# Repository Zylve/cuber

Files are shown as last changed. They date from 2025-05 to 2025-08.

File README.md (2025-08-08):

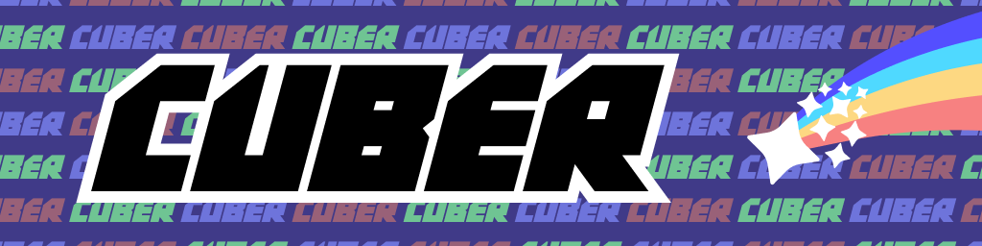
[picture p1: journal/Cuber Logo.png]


# Cuber
Cuber is an automatic rubiks cube robot that can read the state of a 3x3 cube and solve it using servo motors.

Cuber was funded by and built for Hack Club's [Highway](https://highway.hackclub.com) program. You can read my journal [here](./JOURNAL.md). 

Want to make your own? Find documentation on how to build it [here](./docs/README.md).

I've spent over 120 hours designing and building Cuber. Read my thoughts [here](./REFLECTION.md). (TBA)

## 3D Model
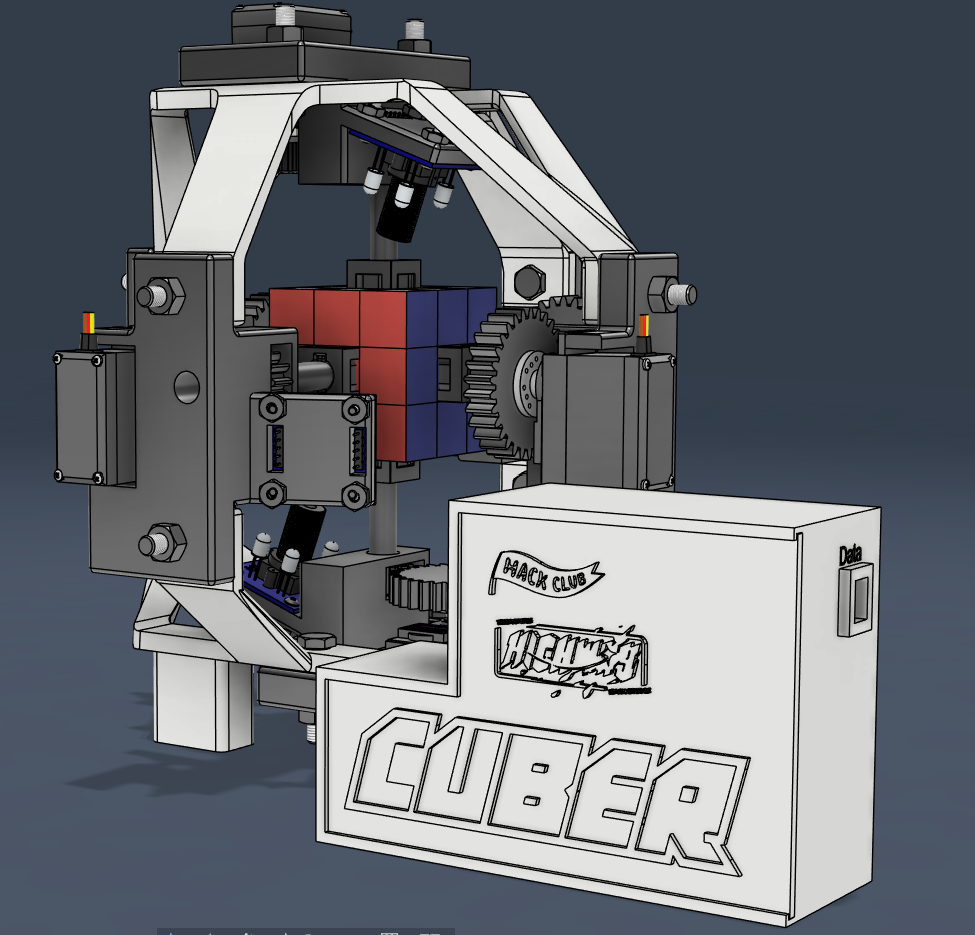
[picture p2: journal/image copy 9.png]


## Wiring Schematic
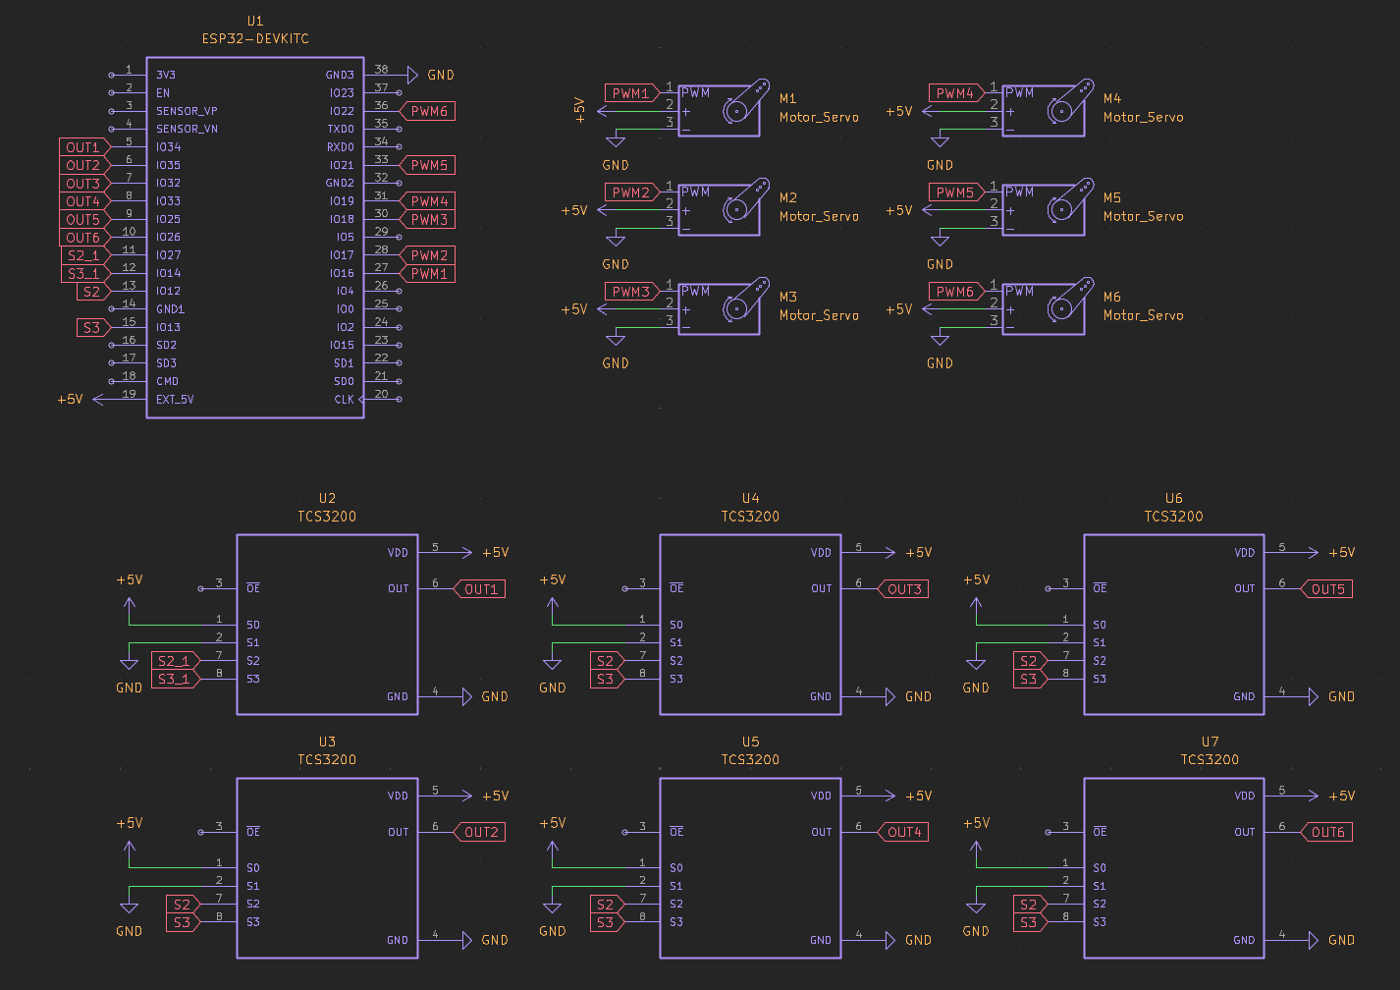
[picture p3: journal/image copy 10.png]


## Physical Project
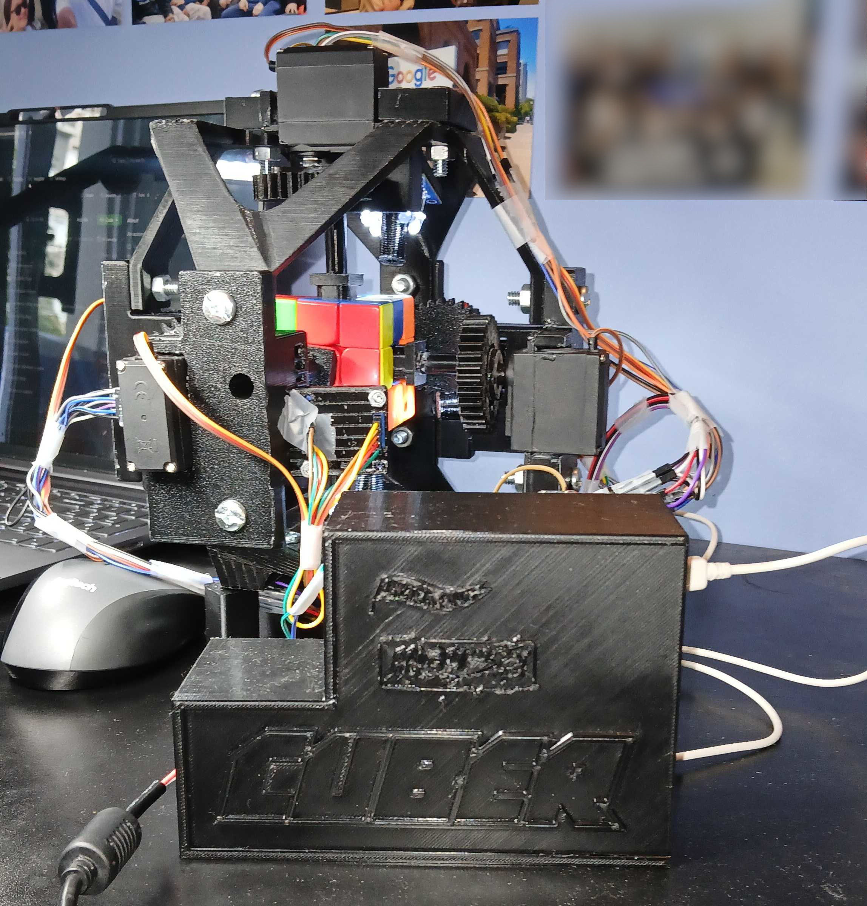
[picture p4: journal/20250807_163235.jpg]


## Bill of Materials
| Item | Amount | Cost (CAD) |
|---|---|---|
| [Esp32 Dev-Board](https://www.aliexpress.com/item/1005006651936701.html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) | 1 | $6.24 |
| [MG996R 180° Stepper Motor](https://www.aliexpress.com/item/1005007032811340.html) | 6 | $32.67 |
| [TCS3200 Colour Sensor](https://www.aliexpress.com/item/1005001625710961.html) | 6 | $24.00 |
| [Assorted Dupont Wires](https://www.aliexpress.com/item/1005004647016228.html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) | 50 | $7.22 |
| [Splice Terminals](https://www.aliexpress.com/item/1005008417745708.html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) | 10 | $8.67 |
| [5V 10A Power Supply](https://www.aliexpress.com/item/4000229912671.html) | 1 | $15.48 |
| [Super Glue](https://www.aliexpress.com/item/1005008238433750.html) | 15g | $24.21
| 1/4-20 & 4-40 Bolts and Nuts | 12 each | $5.00
| PLA Filament | 250g | $6.50 |
| | | |
| **Total** | | **$129.99**|
| **Total USD** | | **$94.56** |

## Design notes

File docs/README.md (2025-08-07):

# Documentation

## Notes
All colours in this project have an ID associated with it. Here are the mappings:
| Colour | ID (0-index) | ID (1-index) | Face |
|:---:|:---:|:---:|:----:|
| White  | 0 | 1 | U |
| Red | 1 | 2 | R |
| Green  | 2 | 3 | F |
| Yellow | 3 | 4 | D |
| Orange | 4 | 5 | L |
| Blue | 5 | 6 | B |

## Hardware
All parts of Cuber were printed in PLA with standard Cura and supports enabled.

The pinion that grabs the cube and the gear were attached to the shaft via press-fit and super glue. The gear attached directly to the servo was aligned using physical guides in the print and super glued.

The colour sensors are attached to the gearbox via 4-40 bolts hardware. This can be done via super glue as well.

The gearboxes are attached to the main nets via 1/4-20 hardware.

## Electronics


Cuber was wired using the following schematic. To prevent larges amounts of current going through the ESP32, you must distribute power directly from the wall. I used wagos to do this, but you can choose a different method. You can view my distribution [here](./WIRING.md).

The S0 & S1 pins on the colour sensors are wired to their secondary set of VCC and GND pins. The S2 & S3 connections are distributed from a single ESP32 pin. All other signal wires are point-to-point to the ESP32.

Note that there exists a separate point-to-point connection for the colour sensor on the up face (S2_1, S3_1). This is because I ran out of wagos.

## Software
### Building & Uploading
Clone the repository.
```bash
git clone https://github.com/Zylve/cuber.git
cd cuber
```

Prepare the platformio project
```bash
pio run
```

To upload the code to the ESP32, connect via USB
```bash
pio run -t upload
```

Setup the python environment
```bash
cd ko
python -m venv .
./bin/pip install pyserial # linux/mac
./Scripts/pip install pyserial # windows
```

### Setting up the code.
Set the correct pins in `include/pins.h`.

#### Servo Calibration
Disable the C_MAIN flag, enable the C_SERVO_INPUT flag and set the servo ID in `include/config.h`. Connect via serial monitor and you will be able to prompt the servo to turn between 0 and 180 degrees. In `src/servos.cpp` you will have to set the correct angles.

```cpp
// Servo 1
ServoConfig servo_config_1 = {
    .axis_positions = {
        {2, 42, 78, 117},
        {2, 38, 78, 117},
        {2, 38, 78, 117},
        {2, 38, 72, 117}
    },
    .square_positions = {20, 35, 56, 71, 93, 109, 132, 149},
    .square_ids = {2, 3, 6, 9, 8, 7, 4, 1} // Different because of the net in the algorithm :/
};
```

The `.axis_positions` is the angle each servo needs to drive to to reach a certain position. The array is in the format of `[from][to]`. Setting the values properly will allow for faster turns as the servo will not undershoot due to friction.

The `.square_positions` is the angle each servo needs to drive to for the colour sensor to point towards each square on the cube. To calibrate, test each angle in order from `.axis_positions[0][0]`, and find the angle that causes the servo to stop such that the dark point of the colour sensor tube is in the middle of the square.

`.square_ids` is the ID of the square mapped to the `.square_positions` array. Note that this is different for the first servo because of how the kociemba library takes input.

#### Colour Sensor Calibration
Set the appropriate values in `src/colours.cpp` for each sensor.

```cpp
ColourConfig config_1 = { // White face sensor
    .white = { // White colour
        .red = {0.30, 0.37},
        .green = {0.30, 0.37},
        .blue = {0.30, 0.37}
    },
    .red = { // Red colour
        .red = {0.48, 1.00},
        .green = {0.00, 0.25},
        .blue = {0.00, 0.20}
    },
    // ...

    .colour_map = {
        .red = {2500, 38000},
        .green = {3600, 24000},
        .blue = {3400, 18000}
    }
};
```

You will have to take the raw readings from the sensors via `sensors[i]->get_colour_raw()`. Rotate each colour on the cube through the sensor and mark down the minimum and maximum values for each colour channel. Set these values as your `.colour_map`.

With the `.colour_map` set, take the normalized readings via `sensors[i]->get_colour_normalized()`. Rotate each colour through various positions and set the proper bands for each channel in each colour.

Note that this will take a lot of trial and error. It took me over 20 hours to get it right. It is still not perfect but I am honestly tired of calibrating the sensors.

Reset the flags in `include/config.h` to enable the main program again.

#### Python Solver
Set the correct serial port in `ko/main.py`
```python
esp32 = serial.Serial(port="COM7", baudrate=9600, timeout=0.1)
```

### Usage

#### Solving
Connect Cuber to wall power and connect the ESP32 via USB to your computer. Upload the program with the main flag enabled.

On a system with port access, run the python script
```bash
./bin/python main.py # linux/mac
./Scripts/python main.py # windows
```
Once connected, Cuber will start reading the faces of the cube. Once it is finished, it will prompt you to enter the colours for any squares that it failed to read. It will display the location (U2, R5, etc) and prompt for the colour (U, R, F, D, L, B). Read through the [notes](#notes) and the [Colour Routine](./COLOURS.md) file for information on that.

After all the colours are entered, it will run the kociemba algorithm, will start running the solution while displaying the moves on the serial monitor.

#### Scrambling
Disconnect Cuber from wall power. Manually scramble the cube. Take note that once connected to power the servos will zero to their starting positions.

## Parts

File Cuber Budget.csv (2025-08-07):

Item | Amount | Cost (CAD)
Esp32 Dev-Board | 1 | $6.24
MG996R 180° Stepper Motor | 6 | $32.67
TCS3200 Colour Sensor | 6 | $24.00
Assorted Dupont Wires | 50 | $7.22
Splice Terminals | 10 | $8.67
Super Glue | 15g | $24.21
5V 10A Power Supply | 1 | $15.48
1/4-20 & 4-40 Bolts and Nuts | 12 each | $5.00
PLA Filament | 250g | $6.50
Total |  | $129.99
Total USD |  | $94.56

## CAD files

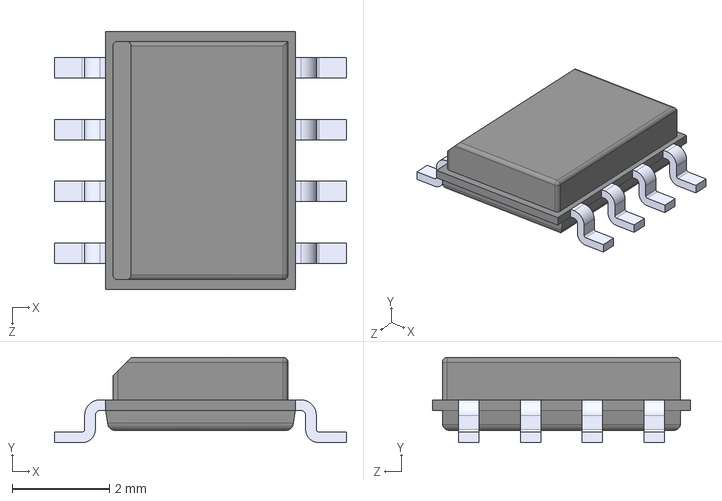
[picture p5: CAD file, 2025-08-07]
CAD/Wiring Diagram/TCS3200/TCS3200.step
6.00 x 1.75 x 5.30 mm

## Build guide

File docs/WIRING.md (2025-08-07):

# Wiring Guide
(This is currently just a reference for myself so if it doesn't make sense, that's okay.)

Colours:
- White: 0 (1)
- Red: 1 (2)
- Green: 2 (3)
- Yellow: 3 (4)
- Orange: 4 (5)
- Blue: 5 (6)

Other:
- 5V: V
- GND: G
- Servo: M
- Colour Sensor: C
- Signal: S# (S0, S1, ...)

5V:
- ESP32
- V0-0,2 (White & Green):
    - V0-0:
        - V0-0M
        - V0-0C
    - V0-2:
        - V0-2M
        - V0-2C
- V1-1,3 (Red & Blue):
    - V1-1:
        - V1-1M
        - V1-1C
    - V1-3:
        - V1-3M
        - V1-3C
- V2-4,5 (Orange & Yellow):
    - V2-4:
        - V2-4M
        - V2-4C
    - V2-5:
        - V2-5M
        - V2-5C

GND:
- ESP32
- G0-0,2 (White & Green):
    - G0-0:
        - G0-0M
        - G0-0C
    - G0-2:
        - G0-2M
        - G0-2C
- G1-1,3 (Red & Blue):
    - G1-1:
        - G1-1M
        - G1-1C
    - G1-3:
        - G1-3M
        - G1-3C
- G2-4,5 (Orange & Yellow):
    - G2-4:
        - G2-4M
        - G2-4C
    - G2-5:
        - G2-5M
        - G2-5C

Signal:
- Signal has no specific routings so we don't care about differentiating each wire.

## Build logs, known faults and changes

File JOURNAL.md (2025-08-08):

---
title: "Cuber"
author: "Vuk"
description: "An automatic Rubik's Cube solver"
created_at: "2024-05-17"
---

### Total Time: 116 hours
---

# May 15th: Started work!
Cooked up my idea and started researching the parts lying around in my kit and the school shop.

### Time today: 1 hour
### Time total: 1 hour

# May 17th:
Okay so basically I set up the platformio dev environment and got my esp32 driving an MG996R stepper motor.

https://github.com/user-attachments/assets/8cf88195-3297-4feb-9b49-cdf6550582a8

I've been wanting to create something like this for a while and I bought these components several months ago but never got around to seriously starting work on it. (And now it looks like Purdue beat me to it lol.)

Anyway I think the best way to properly begin this is to setup some goals for ***Cuber:***
- Create an automatic motorized Rubik's Cube solver.
- Have it automatically detect the initial state of the cube using colour sensors.
- Implement an algorithm like *Kociemba's* to solve the cube.
- Have an automatic scrambler to allow continuous action.
- 3D print a custom case to house components, that allows for easy access to the cube.

Wow that is a lot of goals haha.

To keep the kinematics of the cube simple, I will use a similar approach to the students at Purdue and MIT: 6 motors, one for each face of the  (no full cube rotations). To allow for access to the cube, I will allow the housing for each motor to swing out like a flower, letting me swap the cube in and out.

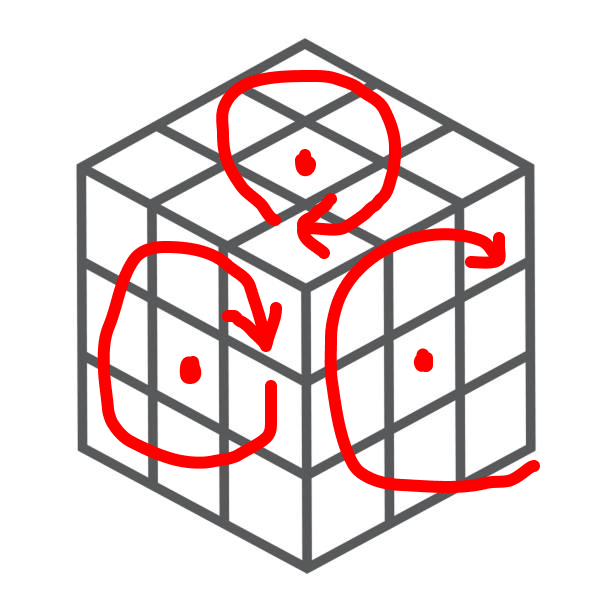
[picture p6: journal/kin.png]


I got 6 TCS3200 colour sensors from my school, and the idea is that one could cover each face of the cube on the corner, and rotate the face at 30° intervals to detect all 12 stickers.

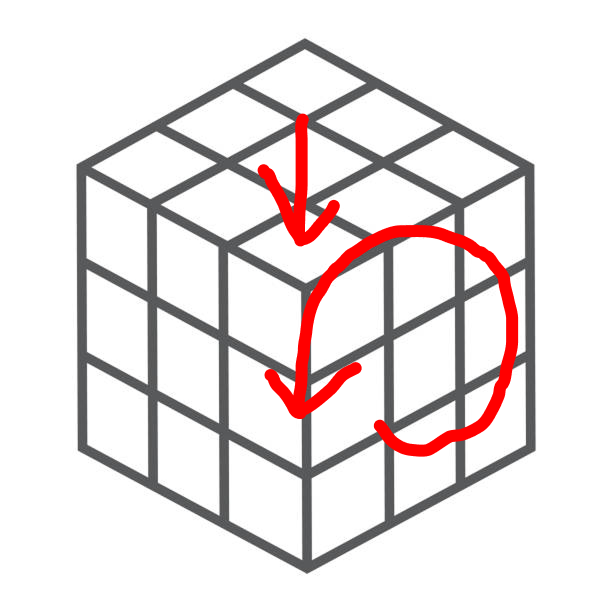
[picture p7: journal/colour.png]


I then imported the MG996R into Fusion 360 and designed a pinion for the Rubiks cube. It will drive the cube sides by slotting into the middle piece. This is when I realized that the motor spline is to small for my 3D printer to print. Instead, I will use the injection molded pinion that came with the motors, and probably superglue the pinion to it or smt idk.

<p float="left">
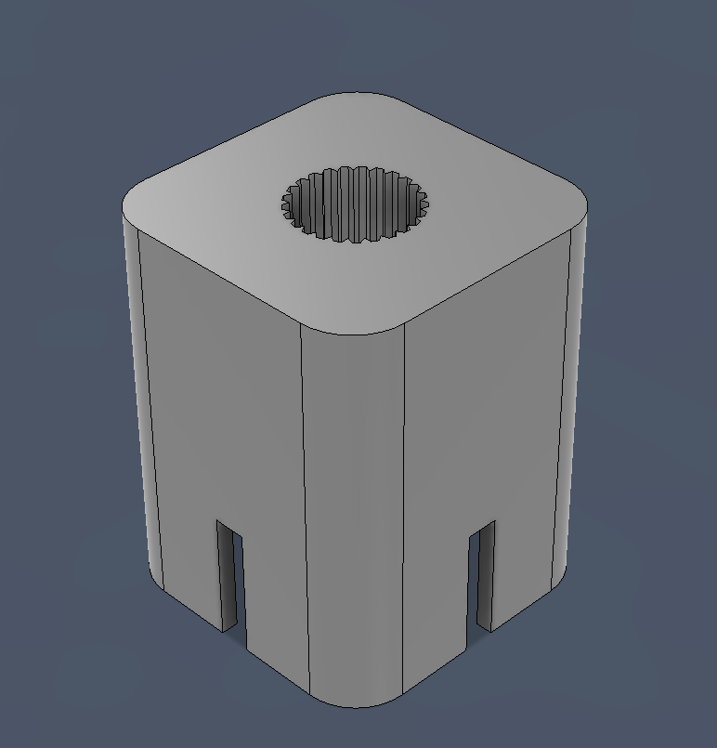
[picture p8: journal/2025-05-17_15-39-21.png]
    
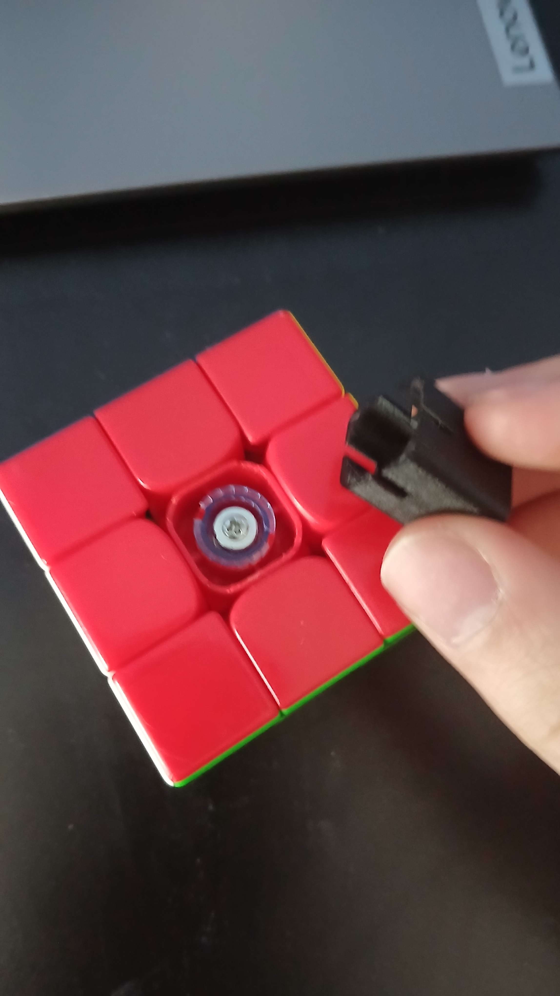
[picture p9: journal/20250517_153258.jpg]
    
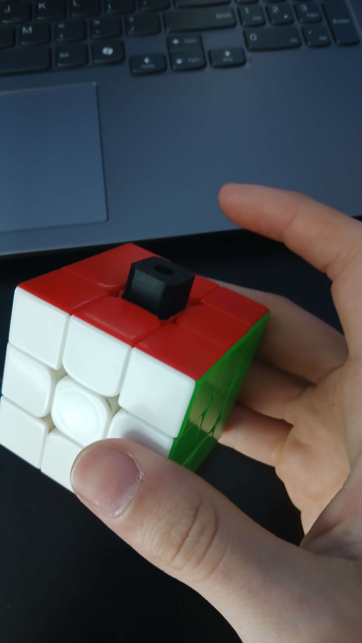
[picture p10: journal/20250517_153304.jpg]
    
</p>

### Time today: 4 hours
### Time total: 5 hours

# May 19th:
Spent like 30 minutes today trying to make PlatformIO actually useable.

I played with my prototype pinion a bit and learned that I need to apply a ton of normal force to allow the sides to rotate.

###### No force (top) vs. force (bottom)
https://github.com/user-attachments/assets/cadc4695-f0eb-4065-a3e3-c17ea3f0df7f

https://github.com/user-attachments/assets/0a5ce550-07eb-4adf-b740-79804e6239e9

I will need to loosen my cube a lot for this, but not so much that it explodes in your face. Lubricant is also needed, I don't know what type to use though. I can buy some specialized stuff from SpeedCubeShop or just douse the cube in some machine oil from my school's shop lol.

I haven't had a lot of time these past couple days but hopefully I will have some more soon!

### Time today: 1 hour
### Time total: 6 hours

# May 23rd:
Finally got some spare time! Jumped into Fusion today and designed a prototype gearbox for the motor & pinion.

Because the version of the MG996R I have has only 180° of rotation, I need to make a step up to allow for full range of motion. I went with a 1:2.5 gear ratio via a 30T pinion and a 12T gear. Not gonna lie the MG996R has a ton of torque—I did the math from the specsheet and I could go up to like 1:8 or something.

Anyway, the 1:2.5 ratio works as all of the angles I need are whole numbers.

<!-- Image.png -->
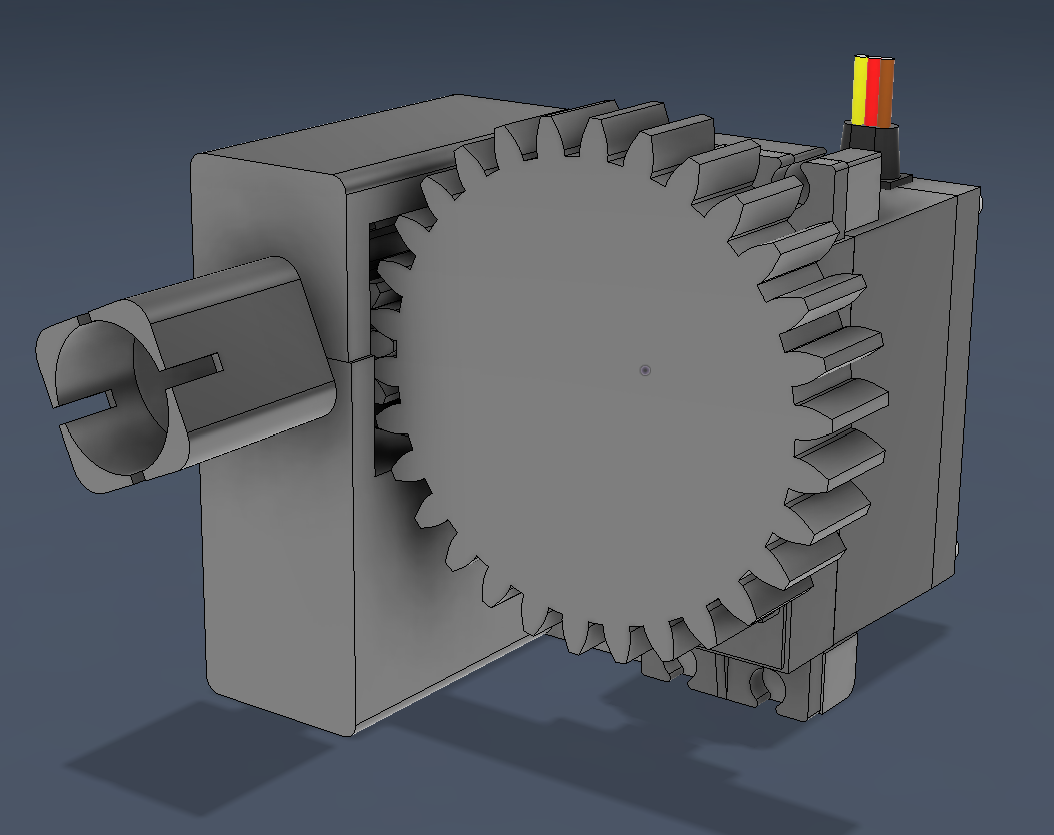
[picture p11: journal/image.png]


I'll be able to 3D print this over the weekend and test it out. If it works, I'll be able to attach 6 of these together to create a full robot. I'm still thinking about how to get the cube in and out though. The flower idea I mentioned early is probably too complex. I'll maybe make the top motor attached via a bolt that you can screw in and out. 

But now that we know we need a large normal force, we may have difficulty getting the cube in and out. When I have time I'll fiddle around with my pinion and see how much play there is and if it would be possible to twist the cube out. Otherwise we may need multiple motors to be unscrewable.

### Time today: 2 hours
### Time total: 8 hours

# May 24th & 25th:
Printed the gearbox. Turns out I suck at superglueing stuff together. Note to future self: sand the prints before gluing lmao.

Got it rotating and stuff. But I'm browning out the ESP32 on just a single stepper motor. Tomorrow I'll be able to take it to school and test it with an actual power supply.

https://github.com/user-attachments/assets/a11832de-1fdf-4844-b957-5d1f5c20488e

### Time this weekend: 4 hours
### Time total: 12 hours

# May 30th

So whats up. I tested the jig with a power supply and theres a couple things I learned:
- I need to make it stiffer so that the gears dont twist out.
- I suck at estimating tolerances.

For most of my testing time, the pieces of the cube were catching on each other, so I had to tighten the cube faces down. It was able to rotate the sides of the cube, but it was quite innacurate due to how much tolerance there was in the pinion and the gears.

I originally created a glue down cover for the pinion to rotate in, but my friend suggested that I make the shaft slide in and have the pinion be press fit.

### Time today: 1 hour
### Time total: 13 hours

# May 31st

Printed some tolerance tests.
- Print in place: 0.5mm
- Print out of place: 0.5mm
- Press fit: 0.3mm

Also designed a new pinion to better fit the cube. Reduced the tolerance between the pinion and the walls of the piece, and made it wrap around the corners. Not sure if the corner pieces actually do anything but maybe it increases the torque lever arm 🤷‍♂️.

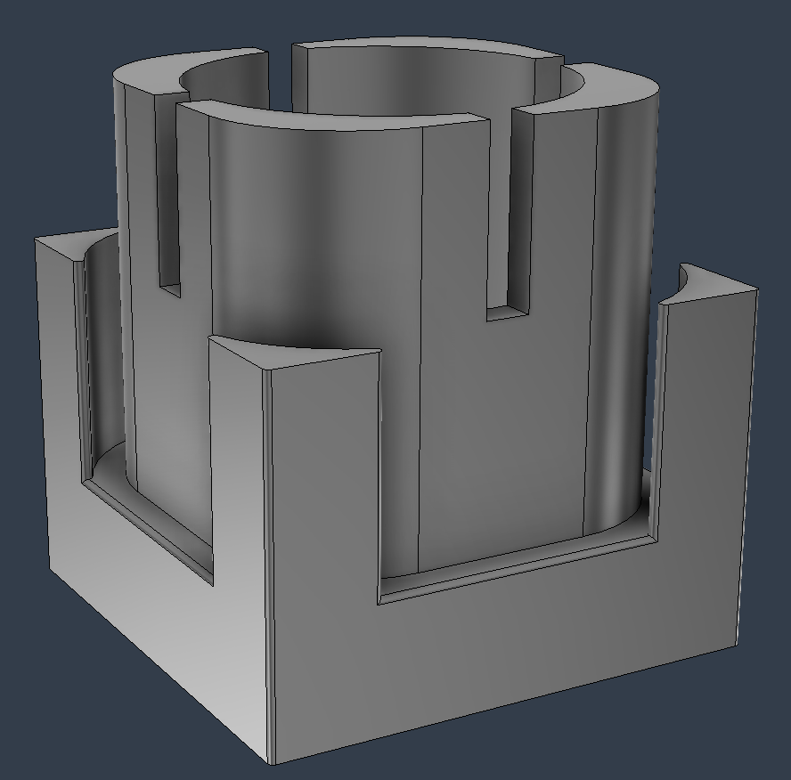
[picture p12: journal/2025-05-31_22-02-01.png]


### Time today: 3 hours
### Time total: 16 hours

# June 1st
Printed out the new gearbox and assembled it together. I need to update it a little as its too close to the face of the cube and the other sides of the cube can't actually rotate lol.

### Time today: 2 hours
### Time total: 18 hours

# June 2nd
Brought it to school and tested it out. Works much better with a lot more backlash. I can still reduce the last bit of it by adding a shaft to the pinion gear, keeping it from rocking side to side. Other than that, its pretty sweet. Something I've noticed is that for some reason the motor isn't linear. 0-90 is the same as 90-180, but 180-270 is much smaller. All stuff that can be changed in software.

https://github.com/user-attachments/assets/d39e9d64-2d36-401b-b0da-273edd4b6365

Hopefully v3 will be the final version of the gearbox. Once I confirm that works then I can start cadding the full assembly.

### Time today: 2 hours
### Time total: 20 hours

# June 6th
Spliced this power supply to power my esp32 and motors. It's 5V 10A, and each motor draws 2A maximum. Hooked it up and it works! I also looked into the specs of the jumper wires I was using and i could power up to 2 motors at a time. (22 AWG, 4A).



### Time today: 1 hour
### Time total: 21 hours

# June 7th
Started playing with the colour sensors. I tried using a library and wasted hours getting it to work. I instead settled to just doing all the fancy stuff manually. I got it able to differentiate between red, green, and blue, but I really need to calibrate the values and tune the thresholds it if I want accurate colours. I think I might need to do this for all 6 sensors.

Colour sensors pmo.

### Time today: 4 hours
### Time total: 25 hours

# June 8th
Dude the colour sensor works. IT WORKS.

I took min and max values for red, green, and blue, and then used this funky map function I found to map it to 0-255. I then used colour normalization to get the ratios of the colours (brightness independent). I then measured each side of the cube, getting the RGB ranges from right up against the cube to about 2 inches away. I could then just iterate over all my colours to find out which RGB band it falls into.

So excited to get this working. I will probably have to recalibrate it when I make the assembly, and also do it for 5 other sensors :(

However, now I know how to do it, so it should be faster next time!

From now I want to focus on integrating a sensor mount into the gearbox, and combining everything into a single 6 motor assembly. I will probably also have to make a wiring diagram. These colour sensors require a lot of pins, (5 exactly) but two of them (the ones that set the frequency) can be shared across all of them, saving 10 pins.

https://github.com/user-attachments/assets/c96f8a81-6cd7-4bb0-83de-4ab9377df998

### Time today: 2 hours
### Time total: 27 hours

# June 9th

Extended the drive shaft so that the cube wouldnt be blocked by the gearbox when turning. Added a mount for the colour sensor to the gearbox. I then also added some mounting holes and arranged the 6 gearboxes into an assembly.

It's really coming together!

I need to make the "net" that connects the 6 gearboxes together. The net will go on the inside of the gearboxes so that you can undo the bolts and just take them out without any maneuvering I also want to figure out how to make the wiring nice. It's gonna be so cooked because of how much there will be. I need 8 wires per gearbox (48 total) + more for splitting my power and ground. At the bottom of the assembly I can make a case for the ESP32. It might even be a good idea to make some buttons for control ("start", "stop"). But yeah. It's gonna be so good.

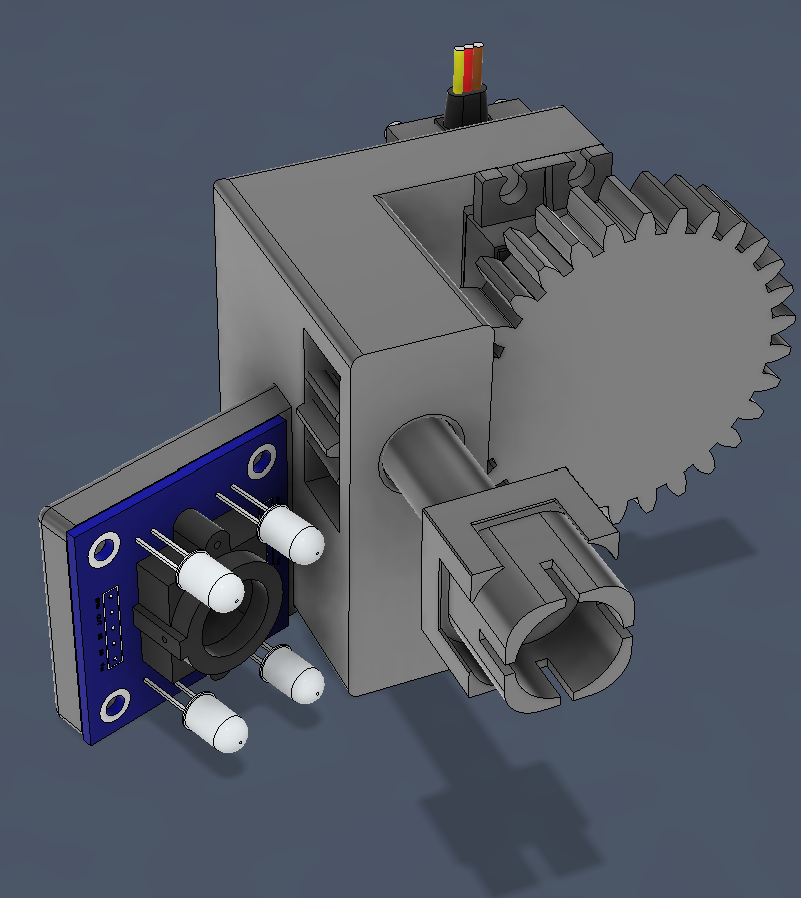
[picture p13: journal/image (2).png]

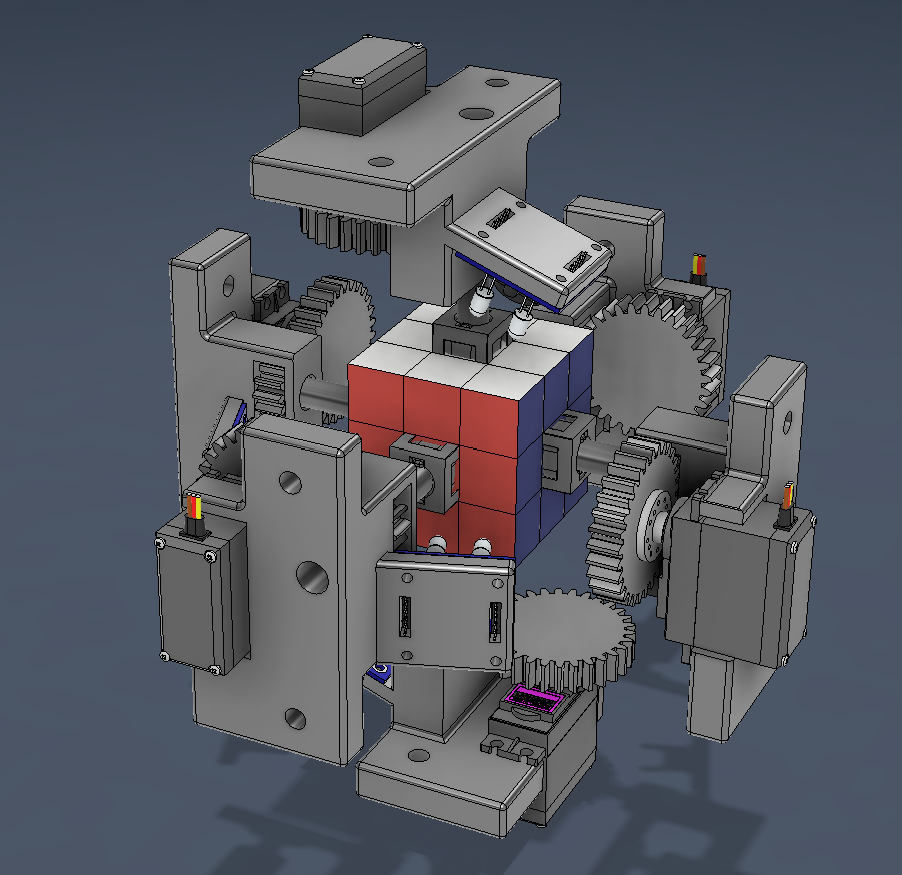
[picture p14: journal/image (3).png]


### Time today: 4 hours
### Time total: 31 hours

# June 10th
Holy lock in.

Made some "nets" that connects the gearboxes together, and a box to store all the electronics. The gearboxes mount to the net via 1/4-20 bolts, and when you unscrew them you can just take it right out with minimal fuss.

The CAD is mostly finished at this point. I had to make a few small modifications to get the colour sensor to fit.

I then made the wiring schematic in Fusion. It turned out a lot cleaner than I expected, but jesus it is a lot of wires. There will be lots of splicing and soldering to do for VBUS, GND, and sensor pins.

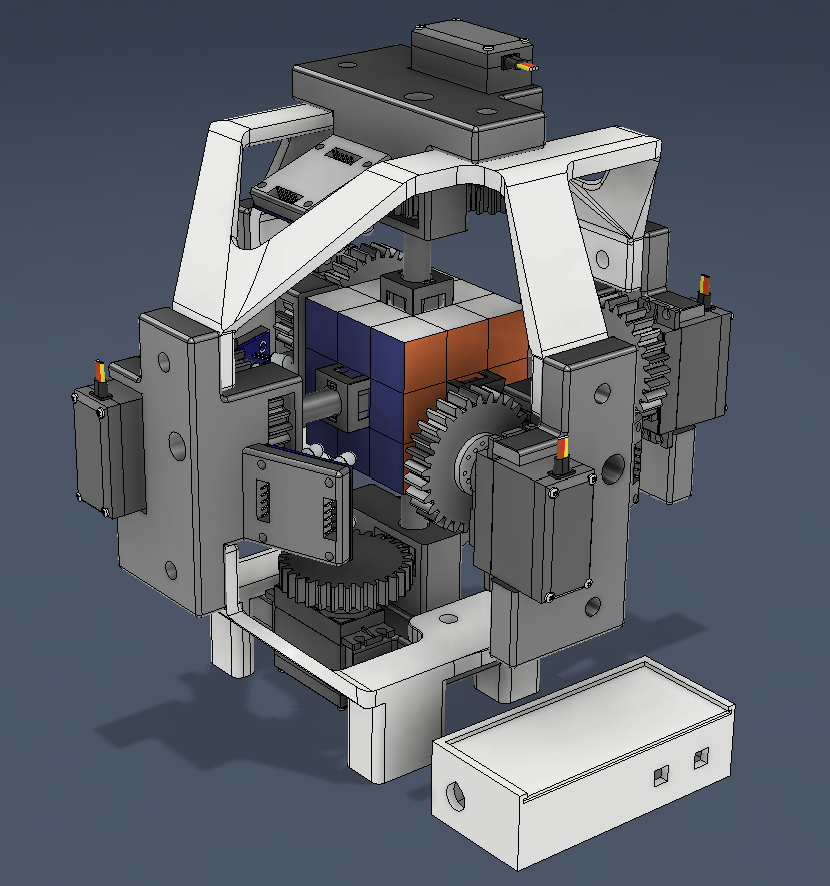
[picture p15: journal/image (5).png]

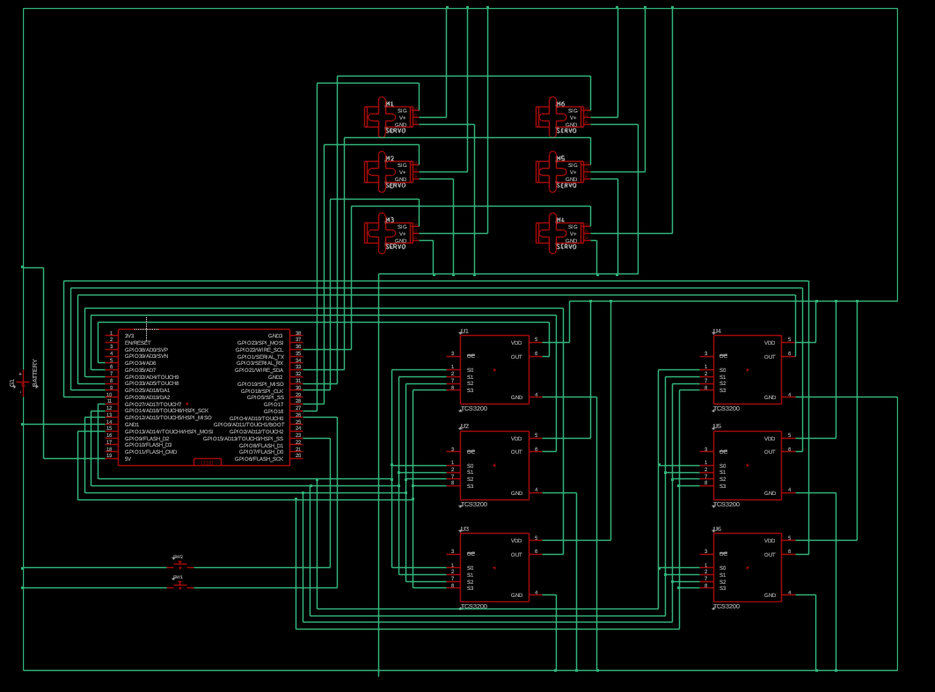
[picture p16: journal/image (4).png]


### Time today: 7 hours
### Time total: 38 hours

# June 11th
Printed a gearbox. These take a lot of time lol. Cleaned it up and removed the supports, then assembled it.

### Time today: 1 hour
### Time total: 39 hours

# June 12th
Printed another gearbox lol. I can really only print one a day because I like sleeping too much.

### Time today: 1 hour
### Time total: 40 hours

# June 13th
Yo so basically I goofed up in the CAD. Turns out the pinion was pressed further into the gear than I thought, so I made everything too close to the cube (As I was assembling the gearboxes with the shaft pressed perfectly into the gear). I had to spend some time modifying the nets to reach out a bit further (0.225") in each direction so that everything would fit. But now it's all good! I'll be able to get a bunch of printing and assembly done this weekend.

### Time today: 2 hours
### Time total: 42 hours

# June 14th
Printed 2 gearboxes.

# June 15th
Printed another gearbox lol.

# June 16th
Printed the final gearbox. I also printed some of the gears but that will take some time.

<p float="left">
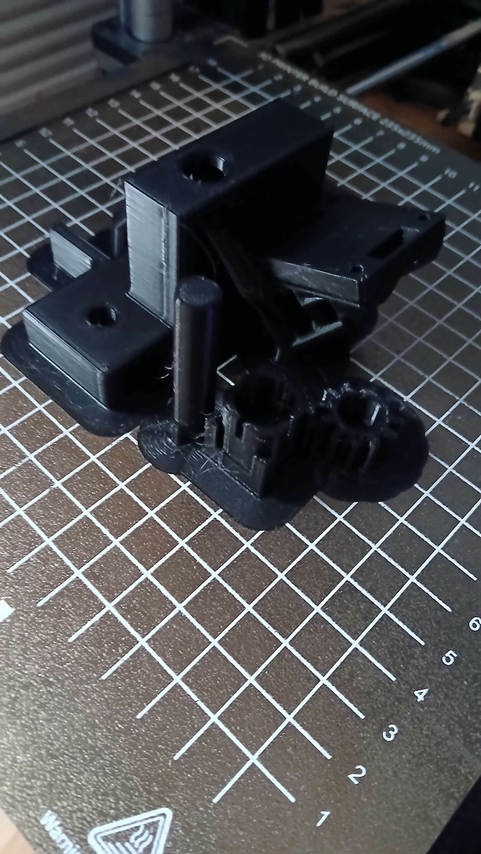
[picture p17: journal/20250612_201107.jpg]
    
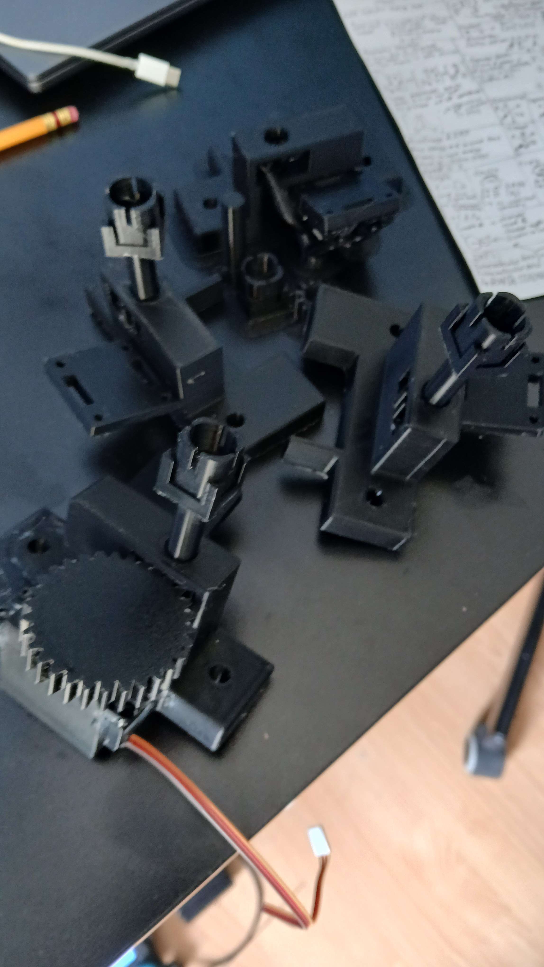
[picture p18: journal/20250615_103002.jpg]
    
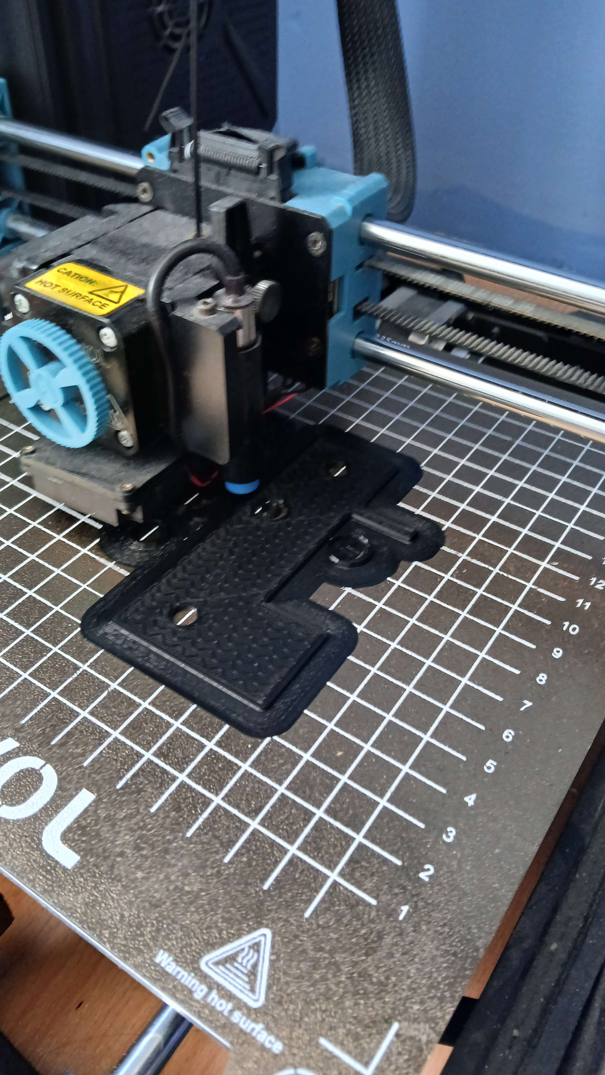
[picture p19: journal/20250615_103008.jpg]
    
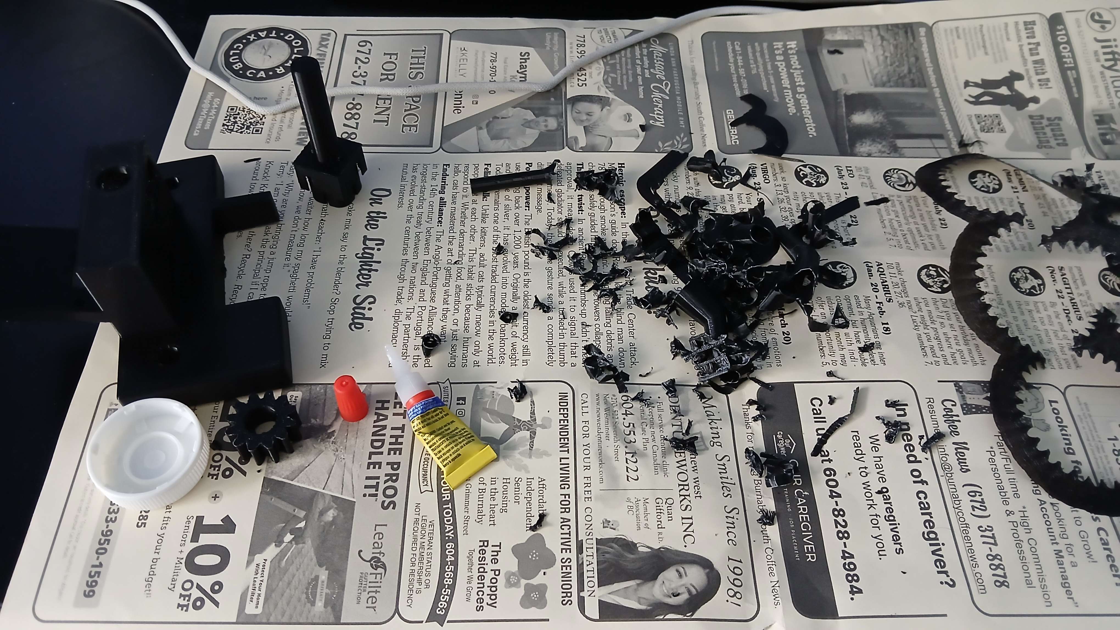
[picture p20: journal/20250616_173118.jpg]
    
</p>

Yo so I did a bunch of boilerplate code for the colour sensors and servos. It's all placeholder values as I can't actually get the real constants until it is fully built.

The plan right now:
- Print gears
- Glue pinions to servos, and servos to gearboxes
- Print the nets
- While printing, write colour detection algorithm and implement Kociemba's
- Assemble the entire thing
- Wire it up & test functionality of each motor and sensor
- Calibrate the sensors
- Calibrate motors
- Test it!

### Time today: 4 hours
### Time total: 46 hours

# June 17th
Yo so I printed the gears 👍

### Time today: 1 hour
### Time total: 47 hours

# June 18th
I printed the bottom net. It took 12 hours but it's done! Looks great and it's fairly stiff so it won't flex under the weight of everything.

<p float="left">
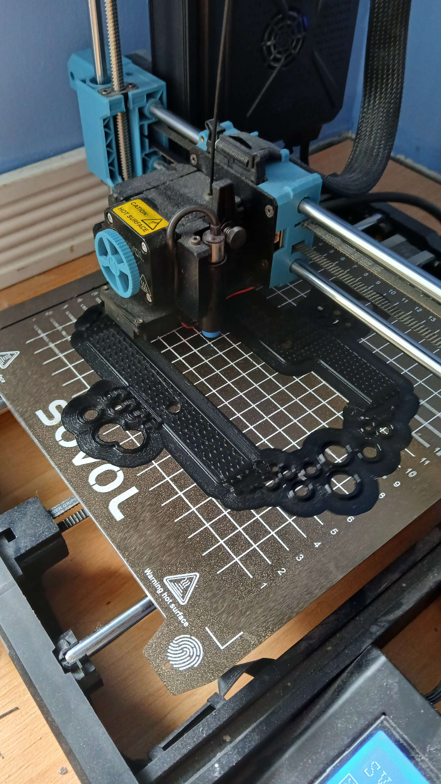
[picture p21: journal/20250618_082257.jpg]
    
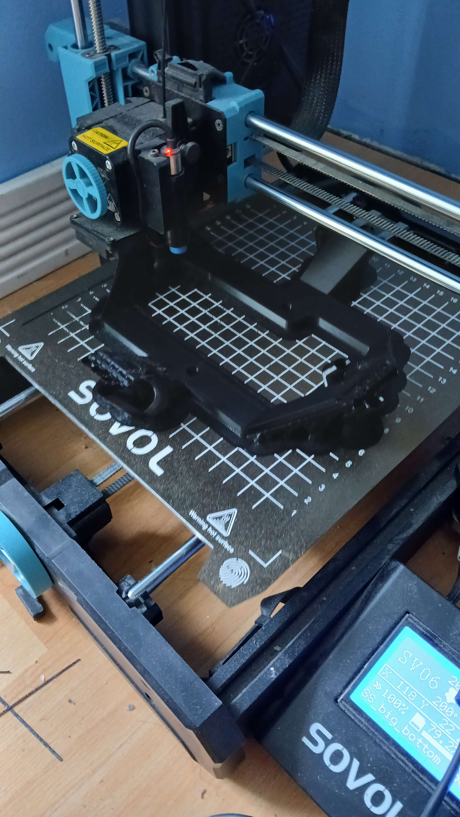
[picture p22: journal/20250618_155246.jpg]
    
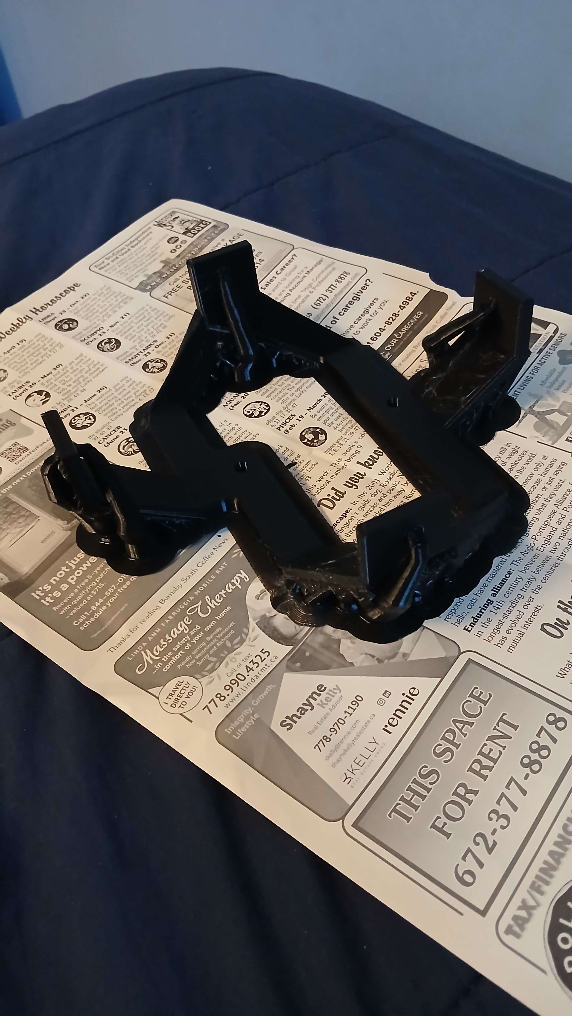
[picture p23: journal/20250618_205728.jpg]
    
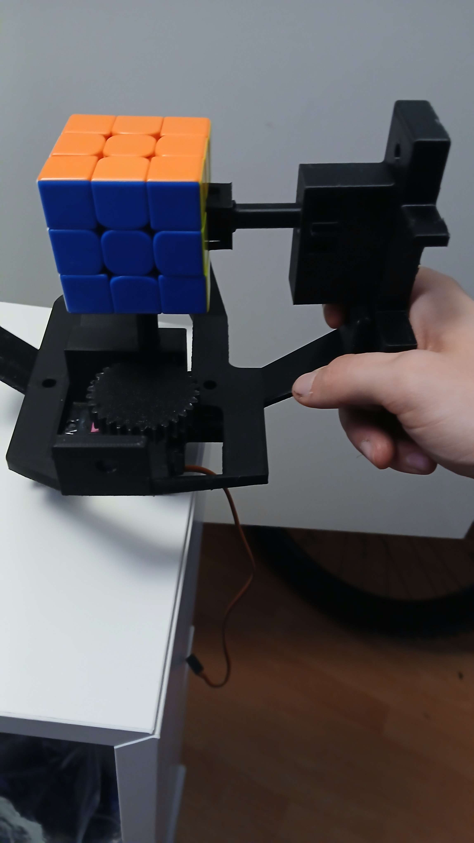
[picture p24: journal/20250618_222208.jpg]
    
</p>

### Time today: 2 hours
### Time total: 49 hours

# June 19th
Me when I forgot to order new filament.

New roll isn't coming until tomorrow. I did get my connectors and wires though so I can start splicing stuff.

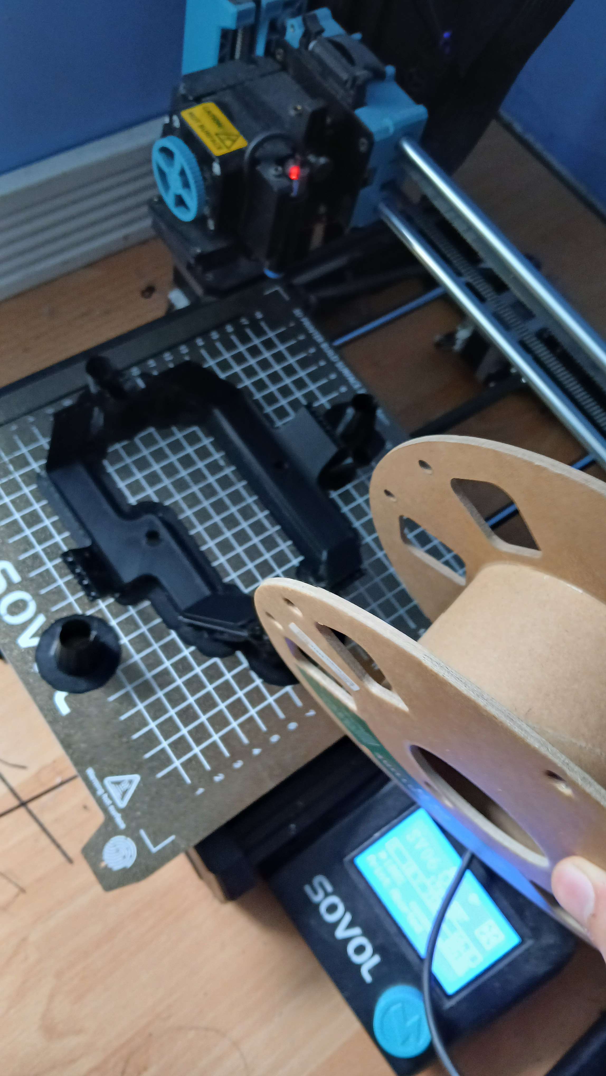
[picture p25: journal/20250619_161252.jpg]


### Time today: 1 hour
### Time total: 50 hours

# June 20th
LAST DAY OF SCHOOL

Anyway Kicad is so much nicer than Fusion 360 wtf. Made this cool new thing that's so much more readable.
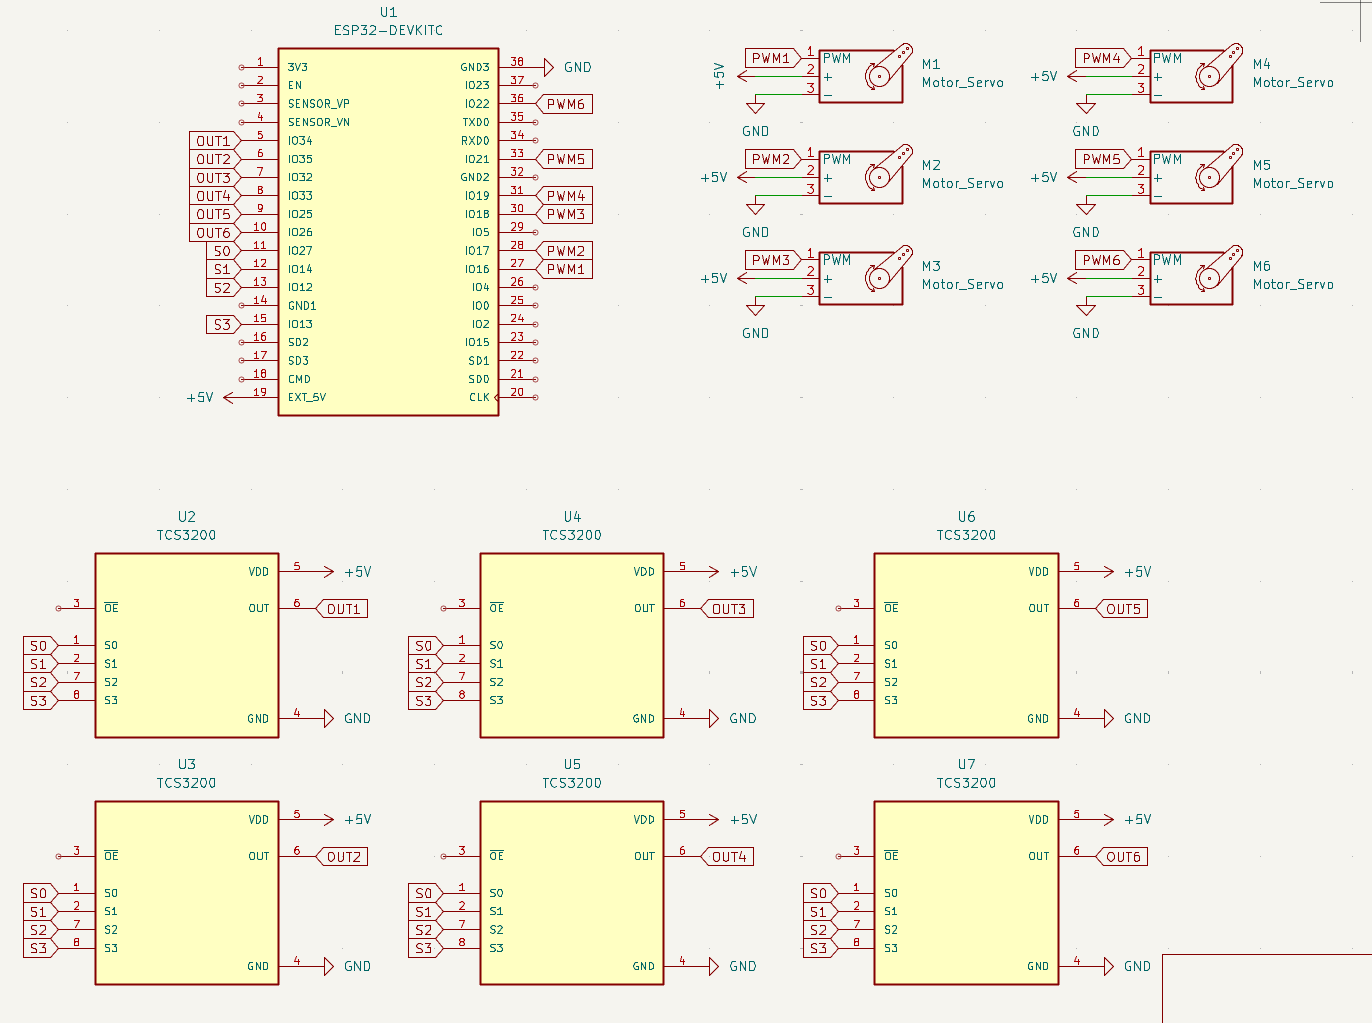
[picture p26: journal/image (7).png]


### Time today: 1 hour
### Time total: 51 hours

# June 21st
I got the filament! Currently printing the top net. I also assembled most of the robot and have attached all the colour sensors. I'm still relaxing from school so I'm not really working that much today.

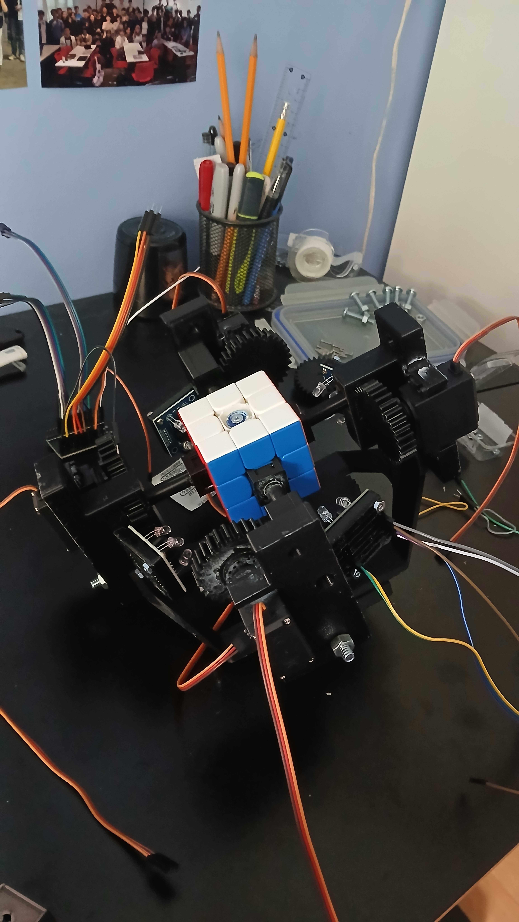
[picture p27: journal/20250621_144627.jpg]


### Time today: 2 hours
### Time total: 53 hours

# June 23rd
Code cleanup. Lowkey forgot the include folder was a thing so I moved all my headers into it.

I then got to work wiring! I found out that I don't need to splice wires to put them into the lever nuts. I hooked up 5V, GND, & PWM for the servos. I still need to wire all the signal wires for the colour sensors.

Wire management is currently a future me problem.

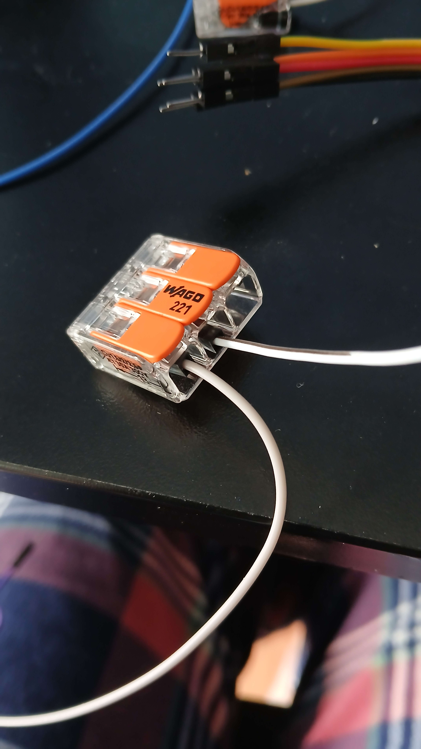
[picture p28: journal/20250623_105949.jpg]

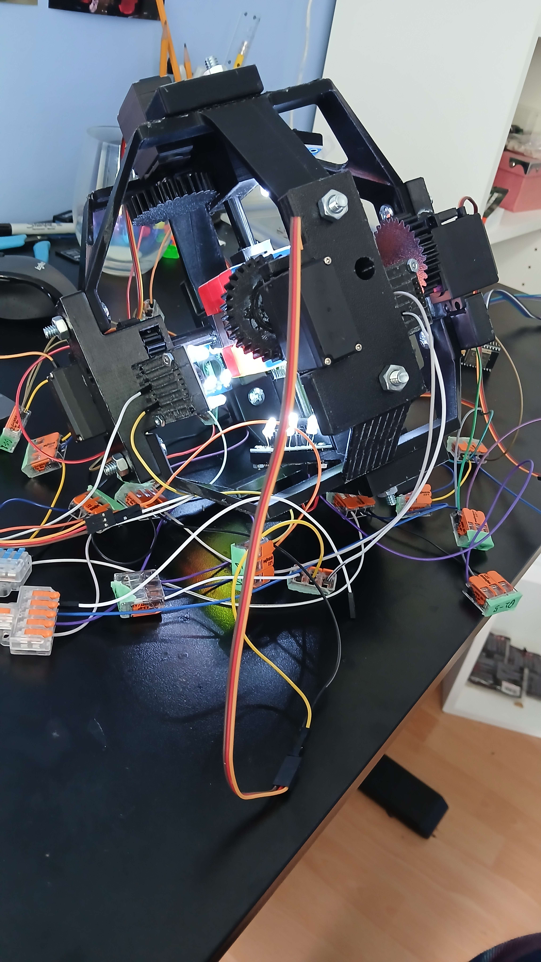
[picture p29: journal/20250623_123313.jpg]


https://github.com/user-attachments/assets/b7c72ac2-09a4-430d-928e-34b1d36eac41

### Time today: 4 hours
### Time total: 57 hours

# June 29th
Got to work testing the servos via code and making sure they all ran.

### Time today: 2 hours
### Time total: 59 hours

# June 30th
Completely overhauled the pwr and gnd wiring to make it much, much nicer. I also found out that specifically one of my servos doesn't have enough torque to turn the face of the cube. I've ordered a new one off aliexpress :(

In the meantime, I can emulate the sixth servo by replacing each instance of U & U' in the steps with a specific algorithm that uses the other 5 faces to rotate it. This is how those commercial solvers work. It does cut down on speed, but it will be very easy to swap once the new servo arrives.

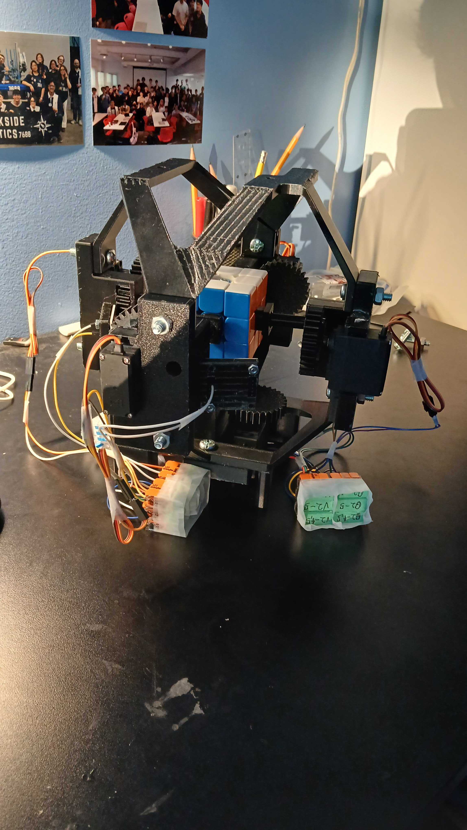
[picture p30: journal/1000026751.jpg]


### Time today: 4 hours
### Time total: 63 hours

# July 1st
CANADA DAY WOOO 🍁🍁🍁

Anyways got stuff working. Found a workaround algorithm while I wait for the sixth servo to arrive.

I tried porting Kociemba's, but it turned out it to be WAY too big for the esp32. So instead Cuber will have the solving logic run via python on a computer, and then relay the information back via the serial port.

### Time today: 6 hours
### Time total: 69 hours

# July 2nd

I got the first cube solve with manual colour input. 90 Seconds. Pretty good for the first solve with one of the motors missing. I want to aim for sub 20 seconds when this is all done. The next step is to hook up & calibrate the colour sensors.

### Time today: 3 hours
### Time total: 72 hours

# July 13th
Hello from Undercity!

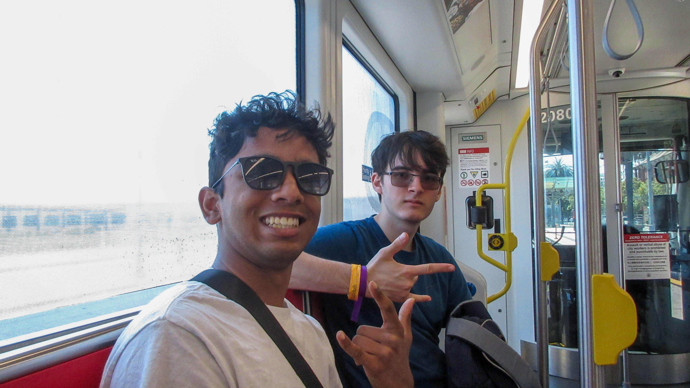
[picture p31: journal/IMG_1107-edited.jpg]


# July 18th
Yo so we back on that grind after an amazing weekend at Undercity.

I changed the way I store servo calibrations, so that it is a grid where you can tune the number based on the current position of the servo.
```cpp
ServoConfig servo_config_1 = {
    .axis_positions = {
    //   0  1   2   3<-To  From
        {7, 50, 85, 126}, // 0
        {7, 50, 85, 126}, // 1
        {7, 44, 85, 126}, // 2
        {7, 44, 78, 126}  // 3
    },
};

servo.write(config.axis_positions[position][target]);
```

I had to recalibrate ALL of the servos 🥀 but now its working. I had a weird bug where two turns in a row would cause it to fall short of it's goal so I added a turn_180 function that makes it move directly to the target.

### Time today: 3 hours
### Time total: 75 hours

# July 19th
I forgot to mention it yesterday, but changing the format of the servo positions also optimized it, since I could make it move further than it needs to, preventing it from slowing down at the end of a turn. I achieved a 20.5 second solve, down from 80 seconds. My PB is 19.5s, so its very close to beating me. When I fully optimize it I expect solves under 15 seconds.

https://github.com/user-attachments/assets/d1df5046-f138-488e-aadc-6c804b91be19

I spent like 3 hours trying to calibrate the colour sensor. My usual method of taking min and max values of RGB on the red, green, and blue faces wasn't working so I instead tried taking the min and max values across all 6 faces. Was able to calibrate it, but didn't have time to test it yet.

### Time today: 3 hours
### Time total: 78 hours

# July 23rd
I got it to differentiate between all the colours! But it's only 1 sensor though. 5 more to go. I was able to test it and it is able to detect the different squares, but it does need to be semi accurate. Lock in this week will be craaazy.

### Time today: 2 hours
### Time total: 80 hours

# July 24th
Pulled out all of the wires and started final wiring. I RAN OUT OF DUPONT JUMPERS. So I need to go buy more 🥀. I have basically a giant wall of wagos so I think it would be nice to 3d print a case for them. It would also help with wiring as I could label and separate the openings.

<p float="left">
    
    
</p>

### Time today: 2 hours
### Time total: 82 hours

# July 28th
Bought more jumpers and extended all of my cables! I'm also gonna hide my wago wall of doom and despair in a cool looking box. I was able to print the lid today.

<p float="left">
    
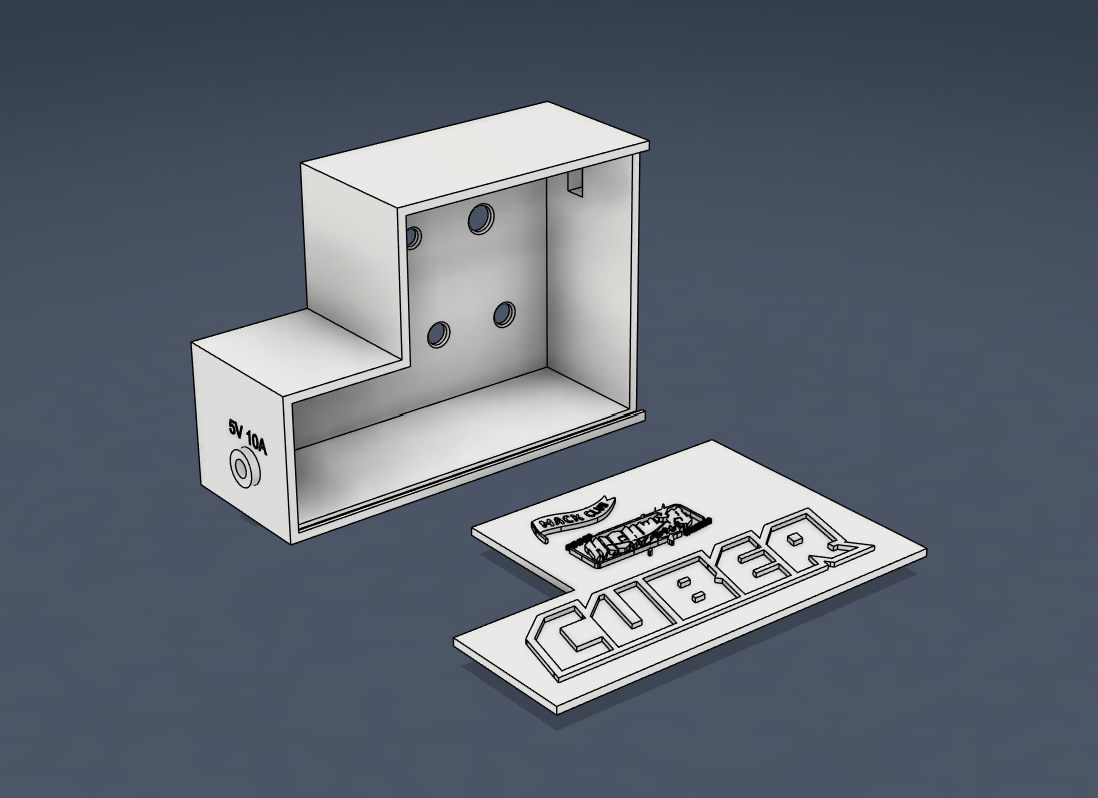
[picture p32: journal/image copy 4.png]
    
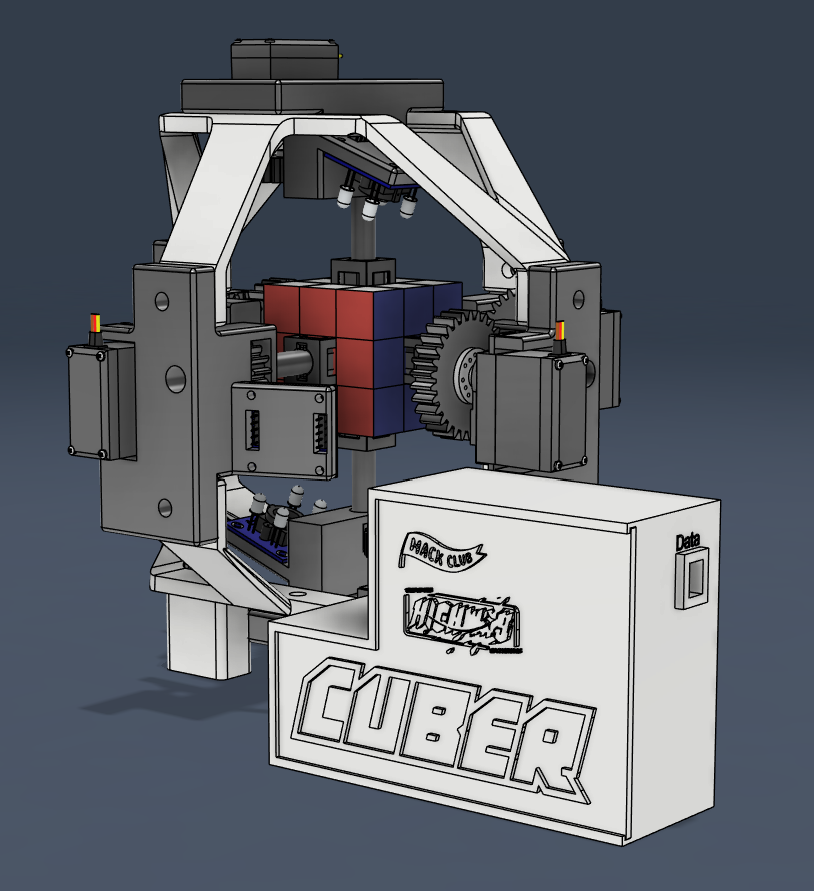
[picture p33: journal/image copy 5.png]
    
    
</p>

### Time today: 4 hours
### Time total: 86 hours

# July 29th
Printed the box! Took 13 hours on my slow ahh printer but its done. Now I can finally do the finished wiring. I also polished the CAD a bit by modelling the fasteners and electronics.

<p float="left">
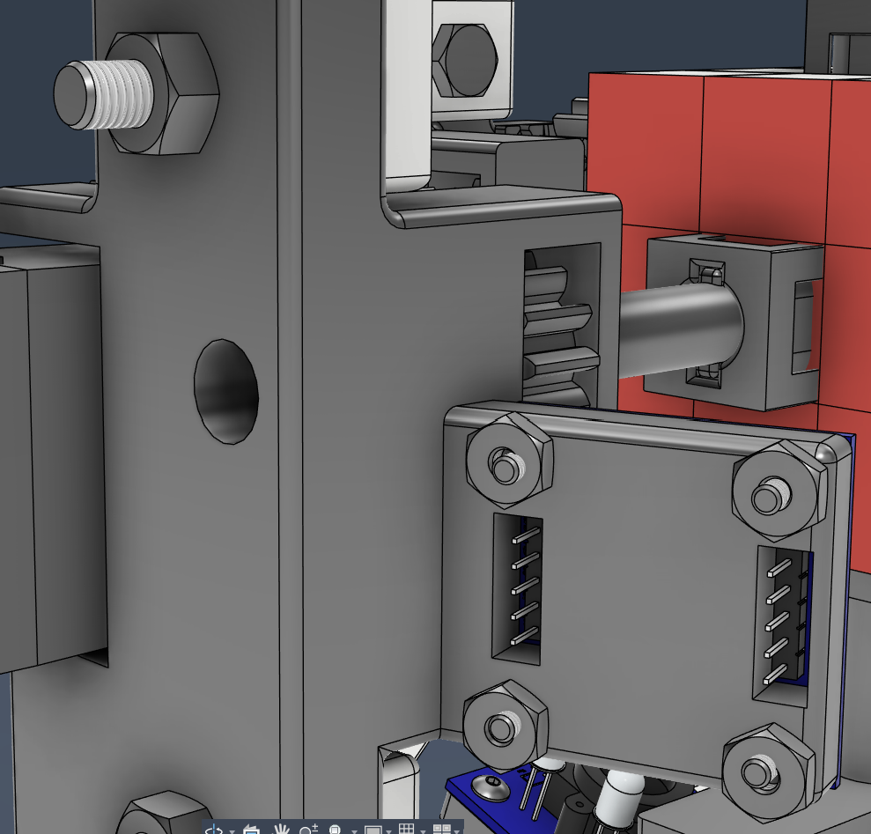
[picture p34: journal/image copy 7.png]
    
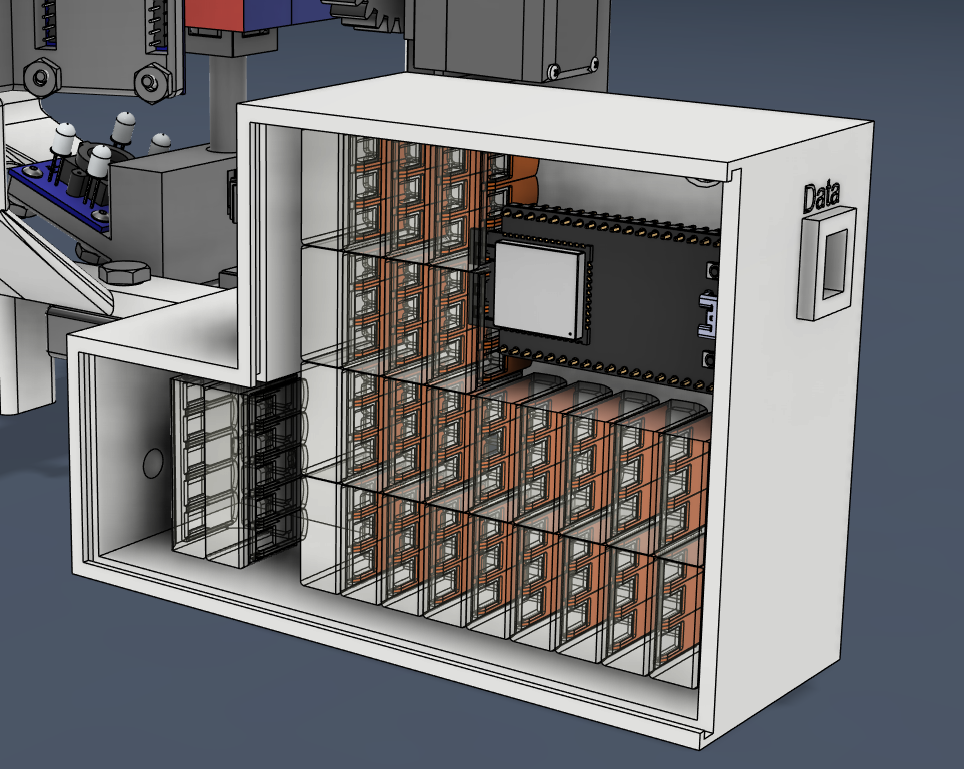
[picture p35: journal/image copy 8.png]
    
    
    
</p>

### Time today: 2 hours
### Time total: 88 hours

# July 30th
Completed the finalized wiring. I somehow keep doing this thing to myself where I try to shove a bunch of electronics into a container that's too small for them.



I then had to do a bunch of cable management.

## Before vs. Before
###### (not a typo)
<p float="left">
    
    
</p>

So what did I learn from this? I fucking suck at critical thinking. I made holes in the box for each type of wire, when it would have been smarter to make 6 holes for the 6 modules, and route the wires internally. That way I wouldn't have to worry about the mess on the outside, all of the wires to a module would go to the same place, and I could thread wires one by one to avoid mixups. Next time I do a project with similar wire requirements, I'll probably make a pcb, and follow this module.

On another note, I have thought about making a Cuber v2! If I did I would definitely use a PCB for wire distribution and use stronger motors. I'd like to beat the human wr (3.08s).

Anyways that's chill. Now I can focus on calibrating the colour sensors.

### Time today: 6 hours
### Time total: 94 hours

# August 1st
Yo so the colour sensor calibrations work, but it all breaks down when doing individual squares as light from the adjacent squares bleeds into it. I create a kind of nozzle that would focus it onto a tiny spot. It improves it a lot, but it isn't quite there. It had a 9mm hole so I scaled it down to 5mm and printed it. Tomorrow I'll test it out.

FYI I have created a self-imposed deadling of this Sunday (August 3rd) to make the colour sensors work. Past that I will give up and create an easy routing for manually inputting the colours.

### Time today: 3 hours
### Time total: 97 hours

# August 2nd
The new nozzle works! It's really consistent. It does reduce the light coming into the sensor a lot, but that doesn't affect it due to the normalization. I wrote a quick one-sided detection routine and calibrated three sides of the cube (top, front, and right). Calibrating it takes so much goddamn time. Still got the other half to do.

Hit the 100 hour mark though!

https://github.com/user-attachments/assets/758a44dc-87e6-4893-bd0c-782bb4a80f7b

### Time today: 7 hours
### Time total: 104 hours

# August 3rd
Got ragebaited by this sensor. I just could not get it to tell apart white and yellow. That's when it hit me: I don't need all 6 sensors. I could get away with 3 and move the squares on other faces into their paths.

### Time today: 4 hours
### Time total: 108 hours

# August 5th
Was still getting ragebaited by this sensor. I deduced that for some reason it wasn't picking up the blue frequency of light properly. I was able to calibrate the remaining two sensors though.

I ended up just writing an algorithm to detect the squares on the back face by moving them to the top and right faces for detection.

I also had some shoddy wiring on the front sensor, but I could not for the life of me figure it out, so I used the same method for it as well.

I had an issue with the power supply to the left face motor, so I disconnected it and spliced it into the right face motor :/

A lot of issues, however I got full colour detection and solving working! Sometimes it fails to pick up colours, so I put a manual input that would catch those and ask you for the colour after the routine is done.

Right now it's just optimization of the solving. Aiming for sub 10, will be happy with sub 15.

Video of first colour detection + solve (on the slack):
https://hackclub.slack.com/files/U06SYK3M62J/F0994RHQTKL/20250805_202403.mp4

### Time today: 8 hours
### Time total: 116 hours

# August 7th
Spent the day cleaning up the repo, and writing documentation.

I also created a pretty sick [youtube video](https://www.youtube.com/shorts/K8QNXNZYxWQ).

### Time today: 6 hours
### Time total: 122 hours

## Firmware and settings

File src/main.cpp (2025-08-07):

#include <Arduino.h>
#include <ESP32Servo.h>
#include "pins.h"
#include "colours.h"
#include "servos.h"
#include "config.h"
#include <esp_system.h>

bool connected = false;
void colour_routine_test();
void solve_test();

void setup() {
    Serial.begin(9600);
    pins_setup();

    delay(1000);

    for(int i = 0; i < 6; i++) {
        servos[i]->attach();
        servos[i]->reset();

        delay(1000);
    }

    if(C_MAIN) {
        while(!connected) {
            Serial.println("esp32_connect");
            delay(250);
            if(Serial.available()) {
                String read = Serial.readStringUntil('\n');
                if(read == "pc_connect") {
                    connected = true;
                    Serial.println("connected");
                }
            }
        }

        delay(1000);

        colour_routine_test();

        solve_test();

    }
}

void loop() {
    if(C_SERVO_INPUT) {
        servo_input(C_SERVO_INPUT_ID, C_SERVO_INPUT_SQUARE);
        return;
    }

    if(C_SERVO_TEST) {
        for(int i = 0; i < 6; i++) {
            servos[i]->reset();
            delay(1000);
        }

        for(int i = 0; i < 6; i++) {
            servos[i]->turn_left();
            delay(2000);
        }

        return;
    }

    // sensors[3]->read_colour();
    // auto raw = sensors[3]->get_colour_raw();
    // Serial.println(String(raw.red) + " " + String(raw.green) + " " + String(raw.blue));
    // auto bounded = sensors[5]->get_colour_bounded();
    // Serial.println(String(bounded.red) + " " + String(bounded.green) + " " + String(bounded.blue));
    // auto normalized = sensors[3]->get_colour_normalized();
    // Serial.println(String(normalized.red) + " " + String(normalized.green) + " " + String(normalized.blue));
    // auto written_colour = sensors[3]->get_colour_string();
    // Serial.println(written_colour);
    // Serial.println(written_colour  + ": " + String(normalized.red) + " " + String(normalized.green) + " " + String(normalized.blue));
    // Serial.println(written_colour + ": " + String(normalized.red) + " " + String(normalized.green) + " " + String(normalized.blue) + " | " + String(raw.red) + " " + String(raw.green) + " " + String(raw.blue));
}

void colour_routine_test() {
    // URFDLB
    String state[6][9];
    state[0][4] = "U";
    state[1][4] = "R";
    state[2][4] = "F";
    state[3][4] = "D";
    state[4][4] = "L";
    state[5][4] = "B";

    delay(1000);

    for(int i = 0; i < 5; i++) {
        if(i == 2) continue; // Skip F face because of wiring issues that I don't feel like fixing.

        for(int j = 0; j < 8; j++) {
            servos[i]->turn_to_square(j);
            delay(300);

            sensors[i]->read_colour();
            auto normalized = sensors[i]->get_colour_normalized();

            state[i][servos[i]->config.square_ids[j] - 1] = sensors[i]->get_colour_face();

            Serial.println("r:" + sensors[i]->get_colour_string() + ": " + String(normalized.red) + " " + String(normalized.green) + " " + String(normalized.blue));
        }

        Serial.println("r:");

        servos[i]->reset();
        delay(2000);
    }

    /* Offload reading of F face colours to U & R faces because I don't feel like fixing the wiring issues. */
    execute_move("R");
    execute_move("L'");
    delay(1000);

    for(int i = 1; i < 4; i++) {
        servos[0]->turn_to_square(i);
        delay(300);

        sensors[0]->read_colour();
        auto normalized = sensors[0]->get_colour_normalized();

        state[2][servos[0]->config.square_ids[i] - 1] = sensors[0]->get_colour_face();

        Serial.println("r:" + sensors[0]->get_colour_string() + ": " + String(normalized.red) + " " + String(normalized.green) + " " + String(normalized.blue));
    }

    for(int i = 5; i < 8; i++) {
        servos[0]->turn_to_square(i);
        delay(500);

        sensors[0]->read_colour();
        auto normalized = sensors[0]->get_colour_normalized();

        state[2][servos[0]->config.square_ids[i] - 1] = sensors[0]->get_colour_face();

        Serial.println("r:" + sensors[0]->get_colour_string() + ": " + String(normalized.red) + " " + String(normalized.green) + " " + String(normalized.blue));
    }

    servos[0]->reset();
    delay(1000);

    execute_move("R'");
    execute_move("L");
    delay(1000);

    execute_move("U'");
    execute_move("D");
    delay(1000);

    servos[1]->turn_to_square(0);
    delay(500);
    sensors[1]->read_colour();
    auto normalized = sensors[1]->get_colour_normalized();
    state[2][7] = sensors[1]->get_colour_face(); // Pos 8
    Serial.println("r:" + sensors[1]->get_colour_string() + ": " + String(normalized.red) + " " + String(normalized.green) + " " + String(normalized.blue));

    servos[1]->turn_to_square(4);
    delay(800);
    sensors[1]->read_colour();
    normalized = sensors[1]->get_colour_normalized();
    state[2][1] = sensors[1]->get_colour_face(); // Pos 2
    Serial.println("r:" + sensors[1]->get_colour_string() + ": " + String(normalized.red) + " " + String(normalized.green) + " " + String(normalized.blue));

    servos[1]->reset();
    delay(1000);

    execute_move("U");
    execute_move("D'");
    Serial.println("r:");
    delay(1000);

    /* Don't need to flip the state because the order is preserved when going from front to up. */

    /* Offload reading of B face colours to U & R faces because the sensor was mismanufactured and has a screwed up blue range ts pmo. */
    execute_move("R'");
    execute_move("L");
    delay(1000);

    for(int i = 1; i < 4; i++) {
        servos[0]->turn_to_square(i);
        delay(300);

        sensors[0]->read_colour();
        auto normalized = sensors[0]->get_colour_normalized();

        state[5][servos[0]->config.square_ids[i] - 1] = sensors[0]->get_colour_face();

        Serial.println("r:" + sensors[0]->get_colour_string() + ": " + String(normalized.red) + " " + String(normalized.green) + " " + String(normalized.blue));
    }

    for(int i = 5; i < 8; i++) {
        servos[0]->turn_to_square(i);
        delay(500);

        sensors[0]->read_colour();
        auto normalized = sensors[0]->get_colour_normalized();

        state[5][servos[0]->config.square_ids[i] - 1] = sensors[0]->get_colour_face();

        Serial.println("r:" + sensors[0]->get_colour_string() + ": " + String(normalized.red) + " " + String(normalized.green) + " " + String(normalized.blue));
    }

    servos[0]->reset();
    delay(1000);

    execute_move("R");
    execute_move("L'");
    delay(1000);

    execute_move("U");
    execute_move("D'");
    delay(1000);

    servos[1]->turn_to_square(0);
    delay(500);
    sensors[1]->read_colour();
    normalized = sensors[1]->get_colour_normalized();
    state[5][7] = sensors[1]->get_colour_face(); // Pos 8
    Serial.println("r:" + sensors[1]->get_colour_string() + ": " + String(normalized.red) + " " + String(normalized.green) + " " + String(normalized.blue));

    servos[1]->turn_to_square(4);
    delay(800);
    sensors[1]->read_colour();
    normalized = sensors[1]->get_colour_normalized();
    state[5][1] = sensors[1]->get_colour_face(); // Pos 2
    Serial.println("r:" + sensors[1]->get_colour_string() + ": " + String(normalized.red) + " " + String(normalized.green) + " " + String(normalized.blue));

    servos[1]->reset();
    delay(1000);

    execute_move("U'");
    execute_move("D");
    Serial.println("r:");
    delay(1000);

    String temp = "";

    temp = state[5][0];
    state[5][0] = state[5][8];
    state[5][8] = temp;

    temp = state[5][2];
    state[5][2] = state[5][6];
    state[5][6] = temp;

    temp = state[5][3];
    state[5][3] = state[5][5];
    state[5][5] = temp;

    String result = "";
    for(int i = 0; i < 6; i++) {
        for(int j = 0; j < 9; j++) {
            result += state[i][j];
        }

        result += " ";
    }

    Serial.println("state:" + result);
}

void solve_test() {
    String solution = "";

    while(true) {
        String solu = Serial.readStringUntil('\n');

        if(solu.substring(0, 5) == "solu:") {
            solu.replace("solu:", "");
            solu = solu + " ";
            Serial.println(solu);
            solution = solu;
            break;
        }
    }

    Serial.println("Sol parsed");

    int moves = 1;
    for(int i = 0; i < solution.length(); i++) {
        if(solution[i] == ' ') {
            moves++;
        }
    }

    String output[moves];

    int index = 0;
    int start = 0;
    for(int i = 0; i <= solution.length(); i++) {
        if(solution[i] == ' ' || i == solution.length()) {
            output[index++] = solution.substring(start, i);
            start = i + 1;
        }
    }

    Serial.println("moves parsed");

    /*
        U = 0
        D = 5
        F = 2
        B = 3
        L = 4
        R = 1
    */

    for(int i = 0; i < moves; i++) {
        Serial.println(output[i]);
        delay(execute_move(output[i]));
    }
}

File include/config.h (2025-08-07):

#pragma once

#define C_SERVO_INPUT false // Enable manual input of servo angles via serial monitor.
#define C_SERVO_INPUT_SQUARE false
#define C_SERVO_INPUT_ID 1

#define C_SERVO_TEST false

#define C_U_MOVE_TEST false

#define C_SOLVE_TEST false

#define C_MAIN true

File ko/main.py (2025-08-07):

import time
import kociemba
import serial

esp32 = serial.Serial(port="COM7", baudrate=9600, timeout=0.1)

while True:
    data = esp32.readline()
    if not data:
        continue
    
    line = data.decode('utf-8', errors="ignore").strip()
    
    if line == "esp32_connect":
        esp32.write(b"pc_connect\n")
        esp32.write(b"connected\n")
        print("connected")
        break

time.sleep(1)

# U = White
# R = Red
# F = Green
# D = Yellow
# L = Orange
# B = Blue

state = ""

while True:
    data = esp32.readline()
    if not data:
        continue
    line = data.decode('utf-8', errors="ignore").strip()
    if line.startswith("state:"):
        print(line)
        state = line[6:]
        state = state.replace(" ", "")
        print("Parsed state:", state)
        break
    if line.startswith("r:"):
        print(line)


# For every "E" in the state, ask for user input
while 'E' in state:
    index = state.index('E')
    # find the position in terms of face and sticker
    faceid = index // 9
    sticker = index % 9
    faces = ["U", "R", "F", "D", "L", "B"]
    face = faces[faceid]
    position = sticker + 1
    user_input = input(f"Colour for {face}{position}: (U, R, F, D, L, B)").strip().upper()
    # replace E
    state = state[:index] + user_input + state[index+1:]

solution = kociemba.solve(state)

message = "solu:" + solution + "\n"
print("Sending solution:", message.strip())

esp32.write(message.encode())

while True:
    response = esp32.readline()
    if response:
        print("ESP32:", response.decode('utf-8', errors='ignore').strip())
        if response.decode('utf-8', errors='ignore').strip() == "esp32_finish":
            esp32.write(b"pc_finish\n")
            break
    else:
        time.sleep(0.1)

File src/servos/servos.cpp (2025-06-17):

#include "servos.h"
#include "pins/pins.h"

ServoConfig servo_config_1 = {
    .axis_positions = {0, 90, 180, 270},
    .square_positions = {0, 45, 90, 135, 180, 225, 270, 315}
};

ServoConfig servo_config_2 = {
    .axis_positions = {0, 90, 180, 270},
    .square_positions = {0, 45, 90, 135, 180, 225, 270, 315}
};

ServoConfig servo_config_3 = {
    .axis_positions = {0, 90, 180, 270},
    .square_positions = {0, 45, 90, 135, 180, 225, 270, 315}
};

ServoConfig servo_config_4 = {
    .axis_positions = {0, 90, 180, 270},
    .square_positions = {0, 45, 90, 135, 180, 225, 270, 315}
};

ServoConfig servo_config_5 = {
    .axis_positions = {0, 90, 180, 270},
    .square_positions = {0, 45, 90, 135, 180, 225, 270, 315}
};

ServoConfig servo_config_6 = {
    .axis_positions = {0, 90, 180, 270},
    .square_positions = {0, 45, 90, 135, 180, 225, 270, 315}
};

ServoWrapper servo_1(servo_config_1, servo_1_pin);
ServoWrapper servo_2(servo_config_2, servo_2_pin);
ServoWrapper servo_3(servo_config_3, servo_3_pin);
ServoWrapper servo_4(servo_config_4, servo_4_pin);
ServoWrapper servo_5(servo_config_5, servo_5_pin);
ServoWrapper servo_6(servo_config_6, servo_6_pin);

void servos_setup() {
    servo_1.attach();
    servo_2.attach();
    servo_3.attach();
    servo_4.attach();
    servo_5.attach();
    servo_6.attach();

    servo_1.reset();
    servo_2.reset();
    servo_3.reset();
    servo_4.reset();
    servo_5.reset();
    servo_6.reset();
}

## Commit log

2025-05-17 Servo moving & lots of journalling foundations
2025-06-08 Colour sensors pmo
2025-06-11 Budget & Other Stuff
    [Cuber Budget.csv]
2025-06-14 40 Hour mark and net goof up 👺
2025-06-17 Colour Sensor code 💀
2025-06-20 lots of printing and 50 hour mark
2025-06-21 new wiring schematic
    [TCS3200.step, Wiring Diagram.kicad_pcb, Wiring Diagram.kicad_sch]
2025-06-21 Hell yeah
    [Wiring Diagram.kicad_sch]
2025-07-19 Done with servos (?)
2025-07-19 Colour Sensor Calibration
2025-07-24 1 sensor working - 80 hours
2025-07-25 began finalized wiring
2025-07-30 Yesterday + Today
    [Wiring Diagram.kicad_sch]
2025-08-02 more colour calibration kms
2025-08-03 100 hour mark + 50% of the sensors working
2025-08-07 Shorten motor delay and add kociemba since it was broken
2025-08-07 Update kicad files
    [TCS3200.step, Wiring Diagram.kicad_sch]
2025-08-07 Remove pcb
    [Wiring Diagram.kicad_pcb]
2025-08-07 Update BOM
    [Cuber Budget.csv]
2025-08-07 add bolts to bom
    [Cuber Budget.csv]
